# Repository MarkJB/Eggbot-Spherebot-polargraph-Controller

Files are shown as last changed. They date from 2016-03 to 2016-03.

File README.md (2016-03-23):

CC BY-NC-SA 2016 Copyright Mark Benson etc etc

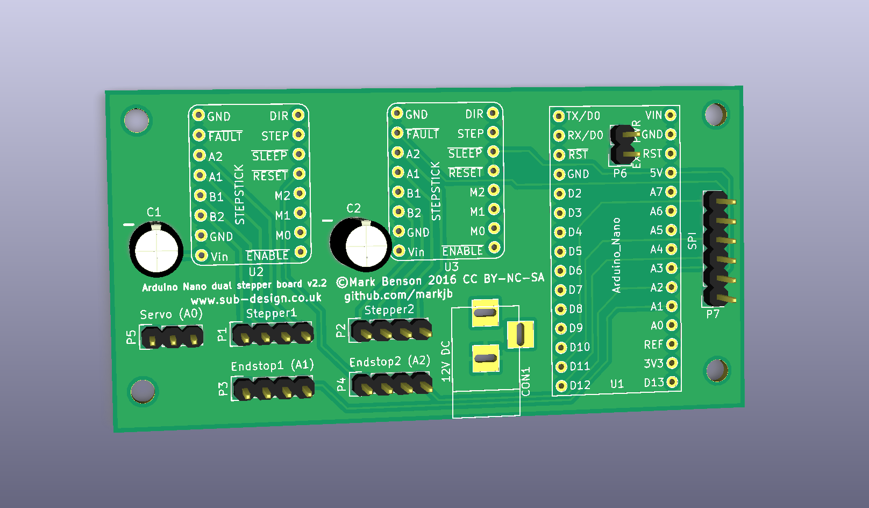
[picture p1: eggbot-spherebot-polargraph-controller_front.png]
PCB


__Note: The v2.1 board is missing a power track between U2 & U3. You will need to solder a jumper wire between the Vin pins or Stepper1 (U2) will not move!__ (This has been fixed with v2.2)

This is my Arduino Nano - Dual Stepstick drawing machine controller PCB for Eggbot/Shperebot/polargraph drawing machines. The reason this uses an Arduino Nano and external stepstick drivers is that they can be found on ebay for not much money and I wanted this to be an affordable way to build the electronics for various drawing machines.

This has been used sucessfully with a 3d printed Eggbot and polargraph. Firmwares adapted for this board available in github.com/markjb. I've also seen it working with the Gocupi firmware.

Micro-stepping is software controlled and both steppers share the same 3 Arduino pins, so you only need configure those 3 pins to set the micro stepping for both steppers.

Assembly should be straight forward.

Orientation of U1, U2 & U3 can be determined by matching the pin names.

Orientation of C1 & C2 is negative to white half of silkscreen.

P1 & P2 (Stepper motors) are wired (from pin 1) A1, A2, B1, B2

P3 & P4 (End stops) are wired for 'Makerbot' style end stops and are wired (from pin 1) Vcc, Gnd, Gnd, Signal

P5 (Servo) is wired (from pin 1) Signal, Vcc, Gnd

BoM

| QTY | Description |
| --- | ---|
| 1 | PCB |
| 1 | Arduino Nano (U1) |
| 2 | Stepstick stepper motor driver boards (DRV8825 or A4988) (U2,U3) |
| 2 | 100uF 35v Electrolitic Capacitor (C1, C2) |
| 4 | 8 way female header (U2,U3) |
| 2 | 15 way female header (these are hard to come by, but 16 way headers are much easier to find and will work if you cut off one of the end pins) (U1) |
| 1 | 6 way female header (P7) |
| 4 | 4 way male header (P1,P2,P3,P4) |
| 1 | 3 way male header (P5) |
| 1 | 2 way male header (P6) |
| 1 | 2 way jumper (P6) |
| 1 | DC socket (CON1) |

EXT PWR = External Power. Enables or disables powering the Arduino from the DC supply. I've had a few Arduino Nano clones go up in smoke when used with both external and USB power. Leave the jumper off EXT PWR unless you have a really good reason for wanting to power the Arduino from the DC supply. I had hoped to be able to enable the SPI SD card and load the command queue onto that and run long Polargrapgh drawings from that on DC power alone, but there are issues with firmware size.

End stops are optional. Might be useful on an Eggbot/Spherebot.

Designed in Kicad 4.0.x. Custom kicad libs included.

PCBs manufactured by iTead Studios PCB prototyping service https://www.itead.cc/open-pcb/pcb-prototyping.html

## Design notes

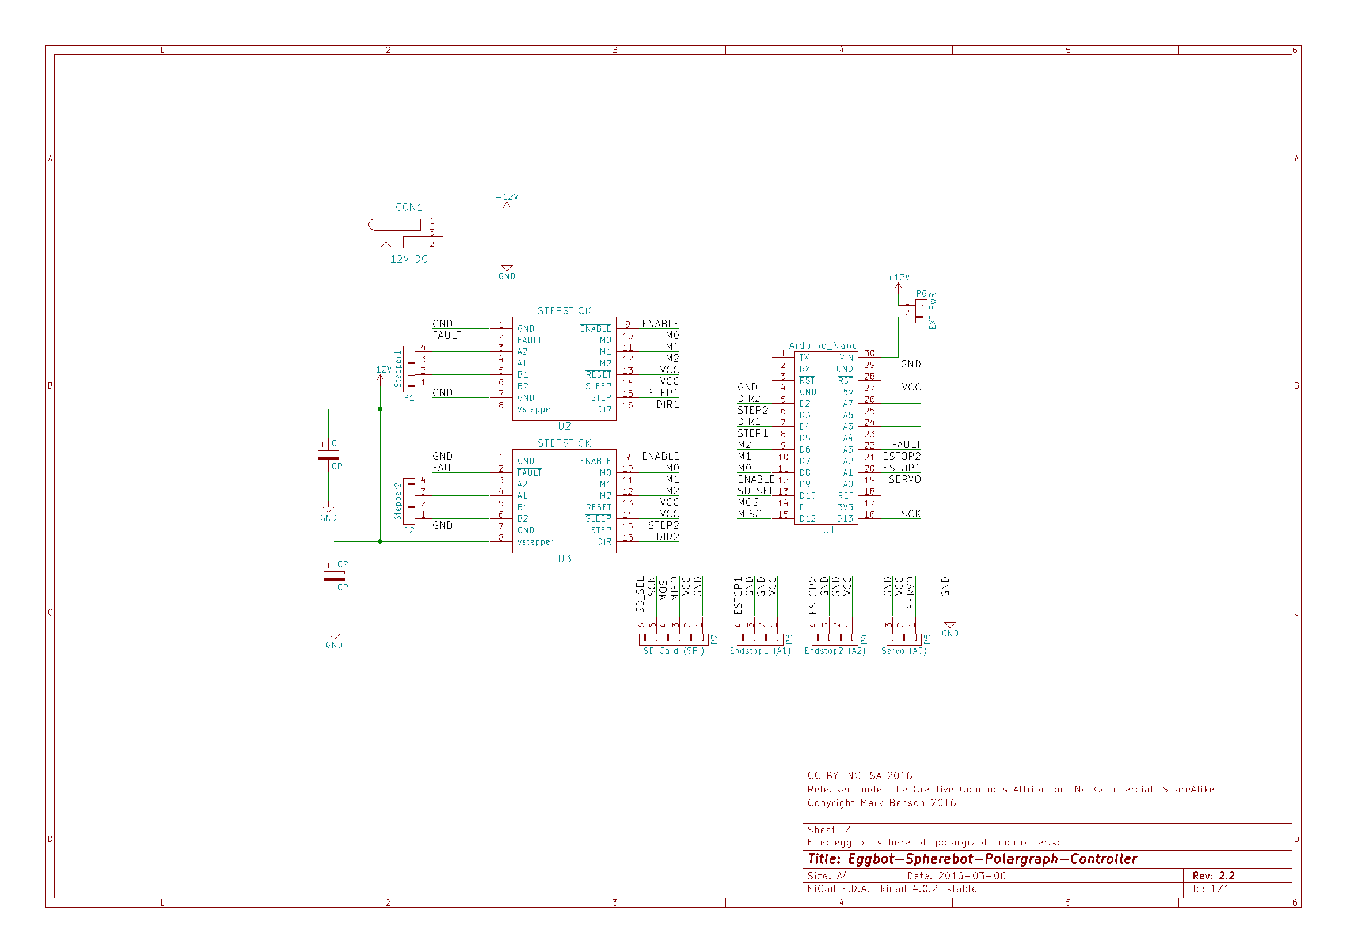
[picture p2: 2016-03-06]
schematic.png

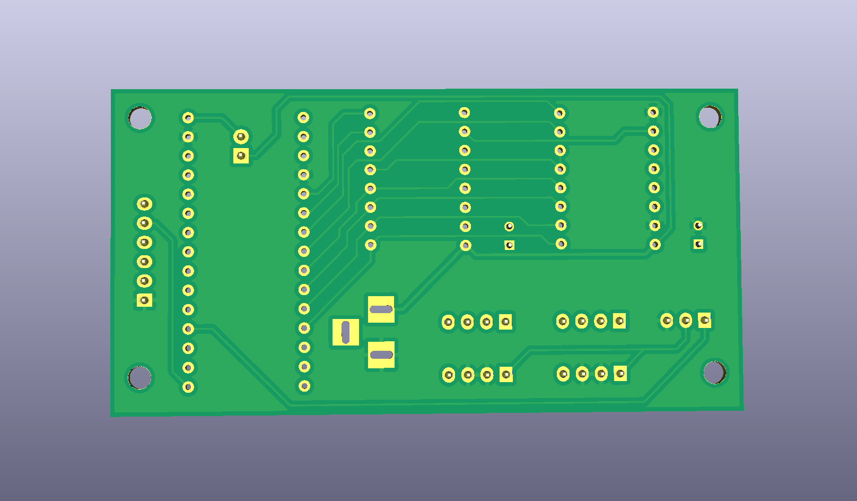
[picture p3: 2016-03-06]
eggbot-spherebot-polargraph-controller_back.png

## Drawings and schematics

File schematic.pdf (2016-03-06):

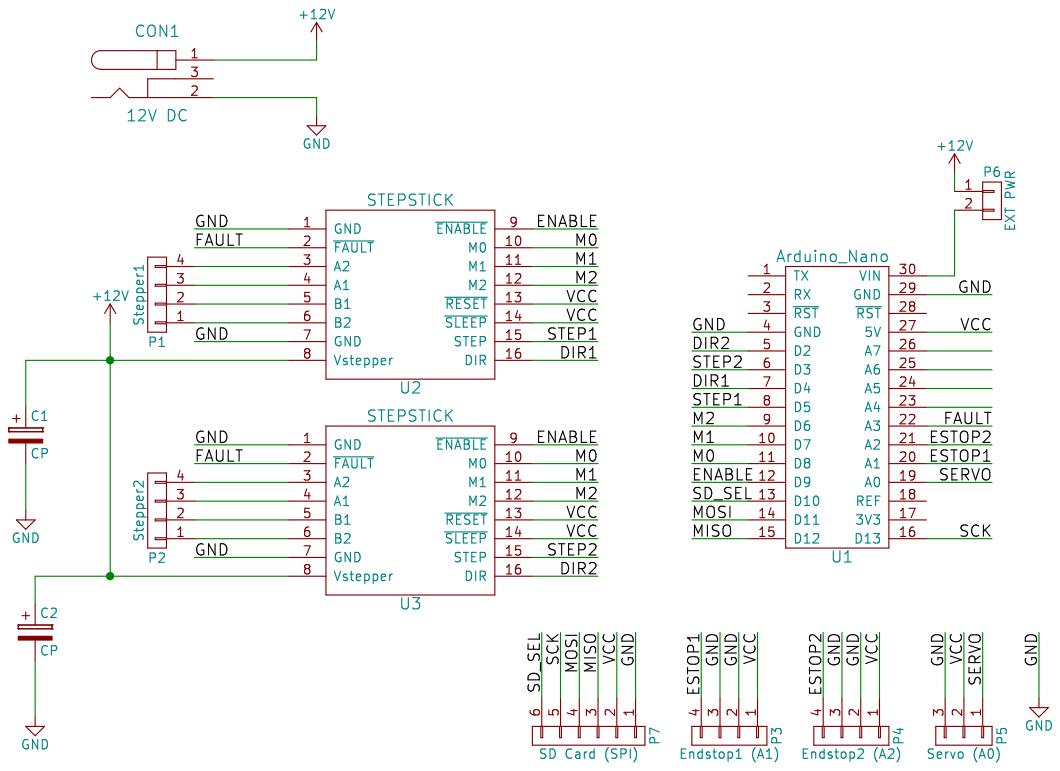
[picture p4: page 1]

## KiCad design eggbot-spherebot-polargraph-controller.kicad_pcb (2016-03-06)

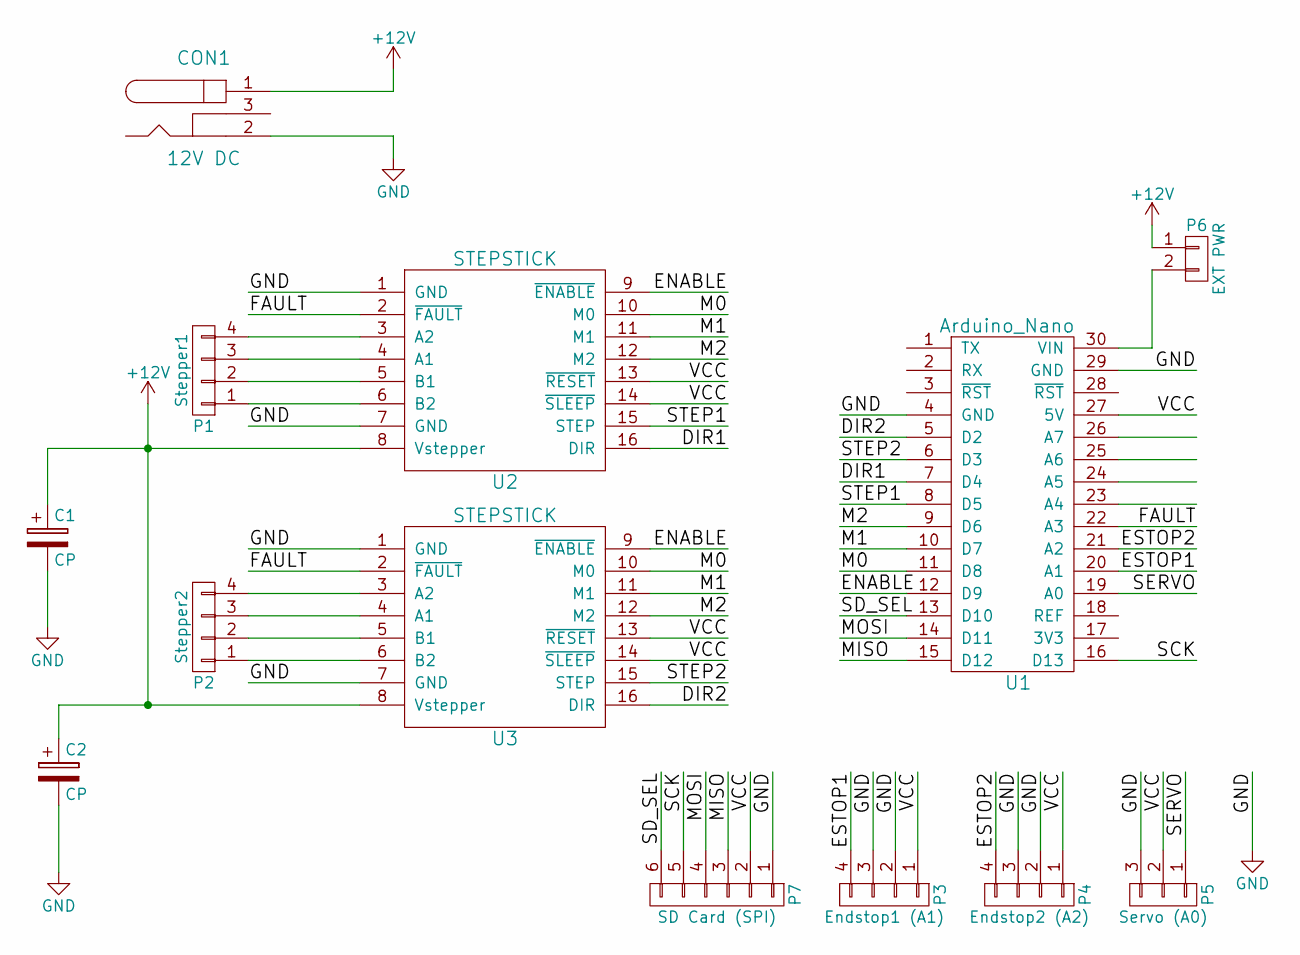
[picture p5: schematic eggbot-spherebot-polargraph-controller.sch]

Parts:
C1, C2: CP; C_Radial_D6.3_L11.2_P2.5
CON1: 12V DC; BARREL_JACK
P1: Stepper1; Pin_Header_Straight_1x04
P2: Stepper2; Pin_Header_Straight_1x04
P3: Endstop1 (A1); Pin_Header_Straight_1x04
P4: Endstop2 (A2); Pin_Header_Straight_1x04
P5: Servo (A0); Pin_Header_Straight_1x03
P6: EXT PWR; Pin_Header_Straight_1x02
P7: SD Card (SPI); Pin_Header_Straight_1x06
U1: Arduino_Nano; Arduino_nano_v3
U2, U3: STEPSTICK; Stepstick

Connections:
+12V: C1.1, C2.1, CON1.1, P6.1, U2.8 (Vstepper), U3.8 (Vstepper)
/DIR1: U1.7 (D4), U2.16 (DIR)
/DIR2: U1.5 (D2), U3.16 (DIR)
/ENABLE: U1.12 (D9), U2.9 (~ENABLE), U3.9 (~ENABLE)
/ESTOP1: P3.4, U1.20 (A1)
/ESTOP2: P4.4, U1.21 (A2)
/FAULT: U1.22 (A3), U2.2 (~FAULT), U3.2 (~FAULT)
/M0: U1.11 (D8), U2.10 (M0), U3.10 (M0)
/M1: U1.10 (D7), U2.11 (M1), U3.11 (M1)
/M2: U1.9 (D6), U2.12 (M2), U3.12 (M2)
/MISO: P7.3, U1.15 (D12)
/MOSI: P7.4, U1.14 (D11)
/SCK: P7.5, U1.16 (D13)
/SD_SEL: P7.6, U1.13 (D10)
/SERVO: P5.1, U1.19 (A0)
/STEP1: U1.8 (D5), U2.15 (STEP)
/STEP2: U1.6 (D3), U3.15 (STEP)
/VCC: P3.1, P4.1, P5.2, P7.2, U1.27 (5V), U2.13 (~RESET), U2.14 (~SLEEP), U3.13 (~RESET), U3.14 (~SLEEP)
GND: C1.2, C2.2, CON1.2, P3.2, P3.3, P4.2, P4.3, P5.3, P7.1, U1.4 (GND), U1.29 (GND), U2.1 (GND), U2.7 (GND), U3.1 (GND), U3.7 (GND)
unnamed: P1.1, U2.6 (B2)
unnamed: P1.2, U2.5 (B1)
unnamed: P1.3, U2.4 (A1)
unnamed: P1.4, U2.3 (A2)
unnamed: P2.1, U3.6 (B2)
unnamed: P2.2, U3.5 (B1)
unnamed: P2.3, U3.4 (A1)
unnamed: P2.4, U3.3 (A2)
unnamed: P6.2, U1.30 (VIN)

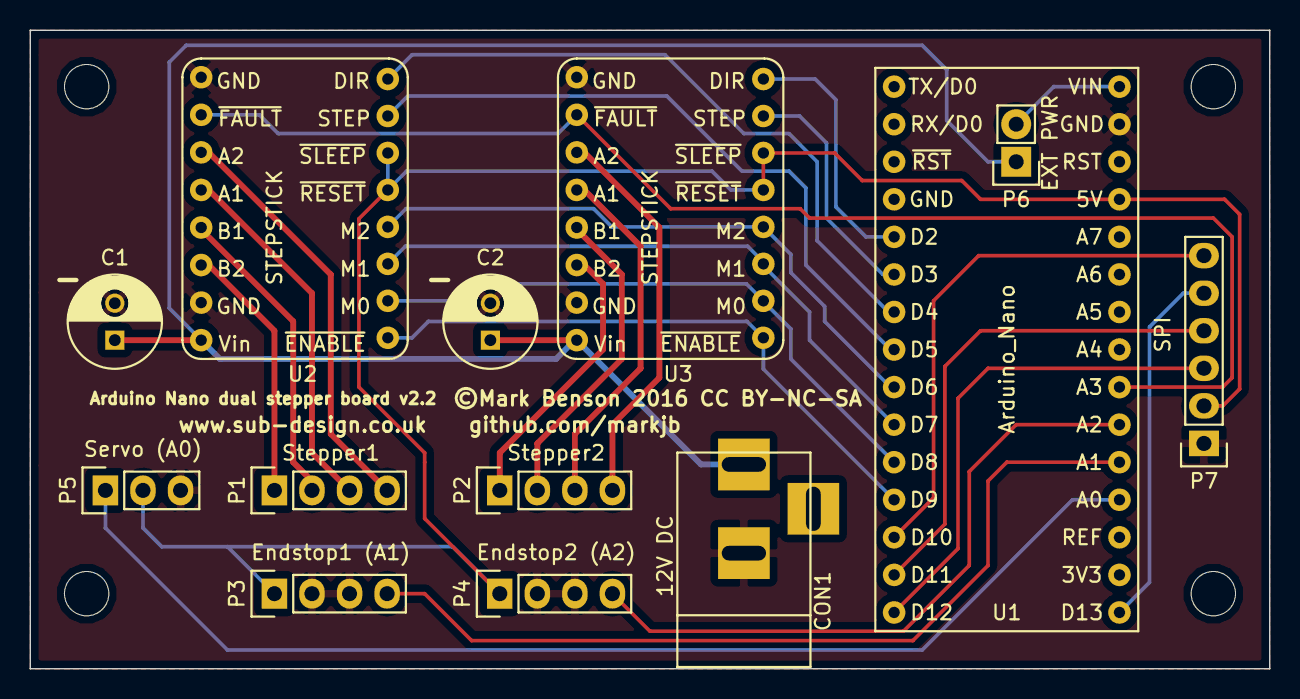
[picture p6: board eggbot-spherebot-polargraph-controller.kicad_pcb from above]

Board: 2 copper layers, 83.8 x 43.2 mm, 13 parts (0 on the bottom side), 28 nets.

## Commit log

2016-03-05 Renamed kicad project - added pdf of schematic
    [eggbot-spherebot-polargraph-controller.kicad_pcb, eggbot-spherebot-polargraph-controller.sch]
2016-03-05 Added schematic png
2016-03-05 Updated 3D renders of PCB
2016-03-06 Updated readme and licence details
    [eggbot-spherebot-polargraph-controller.kicad_pcb, eggbot-spherebot-polargraph-controller.sch]

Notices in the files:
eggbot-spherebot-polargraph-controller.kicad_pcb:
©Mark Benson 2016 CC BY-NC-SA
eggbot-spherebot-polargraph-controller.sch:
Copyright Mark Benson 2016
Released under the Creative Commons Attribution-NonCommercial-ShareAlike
